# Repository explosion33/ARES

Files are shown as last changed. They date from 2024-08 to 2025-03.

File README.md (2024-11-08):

# ARES
Controls and Electronics Repository for SARP's Autonomous Recovery Experimental System (ARES).

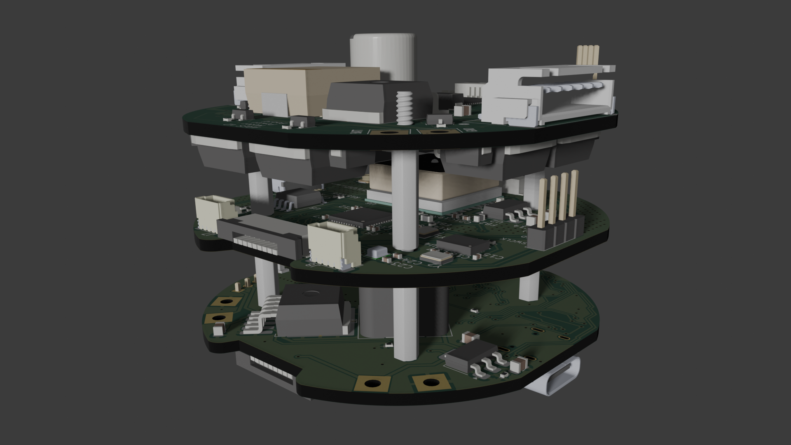
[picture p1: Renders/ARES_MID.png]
ARES Middle Image


## Directory / Ownership

[CC1200 Radio Board / ARES RF Board](https://github.com/stars/explosion33/lists/cc1200-radio-project) | Ethan Armstrong
<br/>
ARES RF board group: KiCad files, Firmware, supporting software

*/CAD*
<br/>
ARES PCB CAD

*/HBridgeTest*
<br/>
HBridge breadboard sample / control code

*/Hardware/Flight_Computer* | Jimmy Fowler
<br/>
ARES Flight Computer PCB Kicad Files

*/Hardware/motor_control_design* | Oliver Buehrer, Ethan Armstrong
<br/>
ARES Actuation (Motor Control) / Power Supply Board Kicad files

*/Renders*
<br/>
ARES PCB Renders

*/Software/Simulation* | Jimmy Fowler
<br/>
ARES simulation code

*/Testbed*
<br/>
ARES Testbed firmware

*/UI*
<br/>
ARES Ground Station UI

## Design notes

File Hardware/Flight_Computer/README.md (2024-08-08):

# RCS_Hardware
SARP 2023 RCS Flight Controller KiCAD project

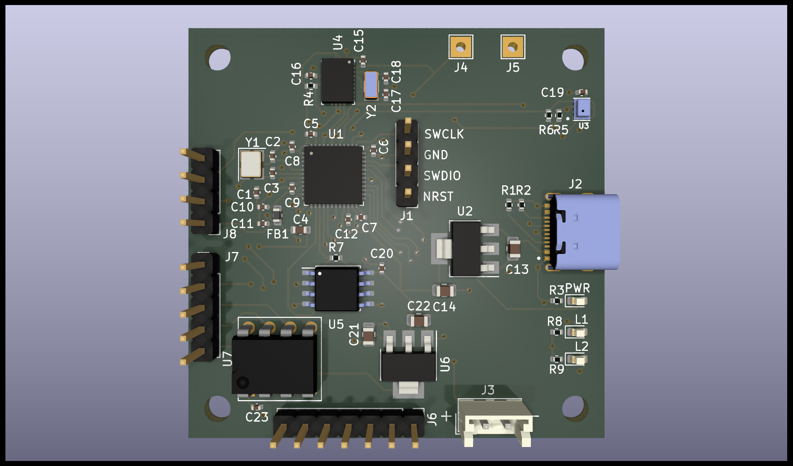
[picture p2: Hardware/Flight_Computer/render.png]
BOARD RENDER


# Components
* STM32F401CCU6
* BNO055
* BMP280
* LIS2HH12 (TODO)
* W25Q32JVXX
* USB-C
* Battery Connector

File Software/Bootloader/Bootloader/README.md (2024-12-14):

# Motor Control / Power Board Testing CodeBase
Codebase in order to test the base functionality of the [MCP Hardware](https://github.com/explosion33/ARES/tree/main/Hardware/motor_control_design)

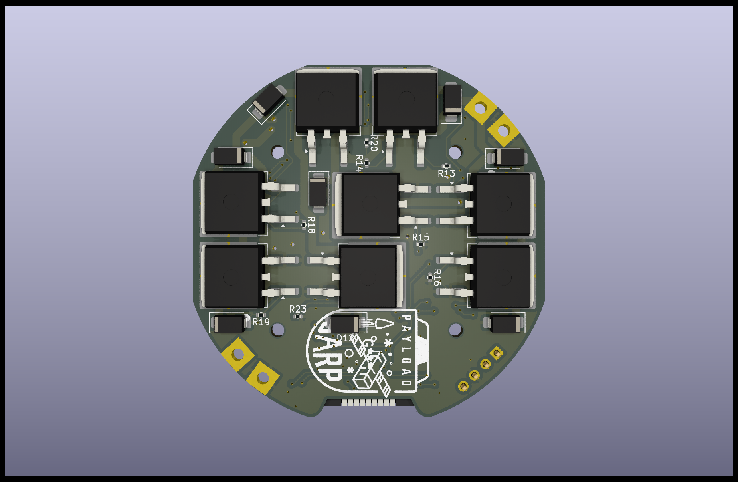
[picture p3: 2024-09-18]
Hardware/motor_control_design/renders/bottom.png

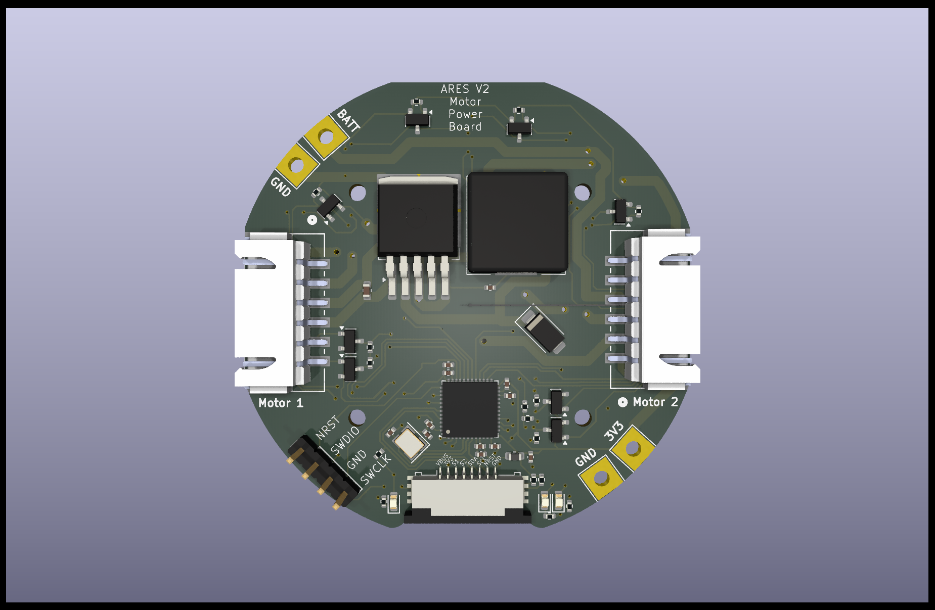
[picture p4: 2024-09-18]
Hardware/motor_control_design/renders/top.png

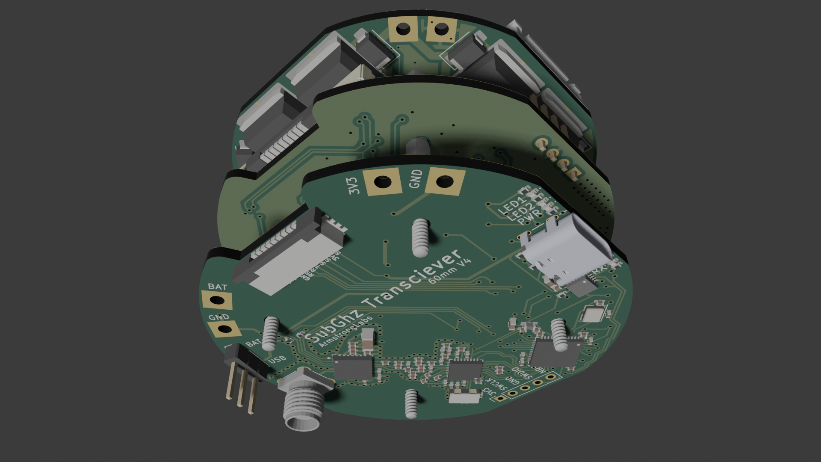
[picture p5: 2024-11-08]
Renders/ARES_BOT.png

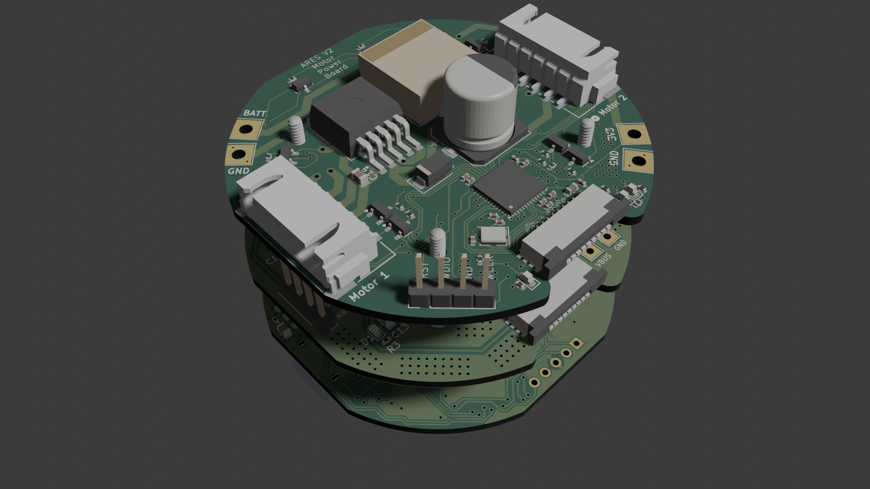
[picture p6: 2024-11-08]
Renders/ARES_TOP.png

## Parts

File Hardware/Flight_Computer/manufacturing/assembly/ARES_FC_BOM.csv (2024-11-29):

Comment | Designator | Footprint | LCSC Part
Antenna | AE1 | Connector_Coaxial:U.FL_Molex_MCRF_73412-0110_Vertical | C5137195
1uF | C10,C11,C21 | Capacitor_SMD:C_0402_1005Metric | C52923
2.2uF | C12 | Capacitor_SMD:C_0402_1005Metric | C12530
22uF | C13,C14 | Capacitor_SMD:C_0805_2012Metric | C5674
22pF | C17,C18 | Capacitor_SMD:C_0402_1005Metric | C466226
10pF | C2,C3 | Capacitor_SMD:C_0402_1005Metric | C32949
10uF | C4 | Capacitor_SMD:C_0603_1608Metric | C19702
100nF | C5,C6,C7,C8,C15,C16,C19,C20,C23,C24 | Capacitor_SMD:C_0402_1005Metric | C307331
10nF | C9 | Capacitor_SMD:C_0402_1005Metric | C15195
LED | D1,D2 | LED_SMD:LED_0603_1608Metric | C12624
LED | D3 | LED_SMD:LED_0603_1608Metric | C2288
LED | D4 | LED_SMD:LED_0603_1608Metric | C2290
120R | FB1 | Inductor_SMD:L_0603_1608Metric | C85831
600R | FB2 | Inductor_SMD:L_0603_1608Metric | C88976
MountingHole | H1,H2,H3,H4 | MountingHole:MountingHole_2.2mm_M2
SWD | J1 | Connector_PinHeader_2.54mm:PinHeader_1x04_P2.54mm_Vertical
TYPE-C-31-M-12 | J2 | USBC:HRO_TYPE-C-31-M-12 | C165948
FC_M/P | J3 | Connector_FFC-FPC:Molex_200528-0080_1x08-1MP_P1.00mm_Horizontal | C132510
5V | J4 | TestPoint:TestPoint_THTPad_2.5x2.5mm_Drill1.2mm
GND | J5 | TestPoint:TestPoint_THTPad_2.5x2.5mm_Drill1.2mm
FC_RF | J6 | Connector_FFC-FPC:Molex_200528-0080_1x08-1MP_P1.00mm_Horizontal | C132510
Conn_01x04_Pin | J7,J8 | Connector_JST:JST_SH_BM04B-SRSS-TB_1x04-1MP_P1.00mm_Vertical | C160390
5.11k | R1,R2 | Resistor_SMD:R_0402_1005Metric | C25906
4.7k | R12,R13,R15,R16 | Resistor_SMD:R_0402_1005Metric | C140158
1k | R3,R8,R9 | Resistor_SMD:R_0402_1005Metric | C11702
10k | R4,R5,R7,R14 | Resistor_SMD:R_0402_1005Metric | C60490
470 | R6,R10,R11 | Resistor_SMD:R_0402_1005Metric | C25167
STM32F401CCU6 | U1 | Package_DFN_QFN:QFN-48-1EP_7x7mm_P0.5mm_EP5.6x5.6mm | C79861
AMS1117-3.3 | U2 | Package_TO_SOT_SMD:SOT-223-3_TabPin2 | C6186
BMP280 | U3 | BMP280:XDCR_BMP280 | C83291
BNO055 | U4 | Package_LGA:LGA-28_5.2x3.8mm_P0.5mm | C93216
W25Q32JVSS | U5 | Package_SO:SOIC-8_5.23x5.23mm_P1.27mm | C82344
PA1616S | U6 | CD-PA1616D:XCVR_CD-PA1616D | C9900146965
16MHz | Y1 | Crystal:Crystal_SMD_3225-4Pin_3.2x2.5mm | C13738
32.768kHz | Y2 | Crystal:Crystal_SMD_3215-2Pin_3.2x1.5mm | C32346

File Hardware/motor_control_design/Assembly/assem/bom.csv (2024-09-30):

Comment | Designator | Footprint | LCSC Part #
10uF Unpolarized capacitor | C1 | C_0402_1005Metric | C19702
10pF Unpolarized capacitor | C2,C5 | C_0402_1005Metric | C32949
100nF Unpolarized capacitor | C3,C4,C6,C8 | C_0402_1005Metric | C307331
2.2uF Unpolarized capacitor | C7 | C_0402_1005Metric | C12530
10nF Unpolarized capacitor | C9 | C_0402_1005Metric | C15195
1uF Unpolarized capacitor | C10,C11 | C_0402_1005Metric | C52923
100uF Unpolarized capacitor | C14 | C_0805_2012Metric | C141660
330uF Unpolarized capacitor | C15 | C_0402_1005Metric | C19702
LED Light emitting diode | D1,D2,D3 | LED_0603_1608Metric | C273598
SS34 40V 3A Schottky Diode, SMA | D4,D5,D6,D7,D8,D9,D10,D11,D12 | D_SMA | C3032484
120R Ferrite bead, small symbol | FB1 | L_0603_1608Metric | C85831
SWD Generic connector, single row, 01x04, script generated (kicad-library-utils/schlib/autogen/connector/) | J2 | PinHeader_1x04_P2.54mm_Vertical
VBAT Generic connector, single row, 01x01, script generated (kicad-library-utils/schlib/autogen/connector/) | J3 | TestPoint_THTPad_4.0x4.0mm_Drill2.0mm
GND Generic connector, single row, 01x01, script generated (kicad-library-utils/schlib/autogen/connector/) | J4,J9 | TestPoint_THTPad_4.0x4.0mm_Drill2.0mm
FC_M/P Generic connector, single row, 01x08, script generated (kicad-library-utils/schlib/autogen/connector/) | J5 | Molex_200528-0080_1x08-1MP_P1.00mm_Horizontal | C124378
Conn_01x06 Generic connector, single row, 01x06, script generated (kicad-library-utils/schlib/autogen/connector/) | J6,J8 | CONN_S6B-XH-SM4-TB_JST
3V3 Generic connector, single row, 01x01, script generated (kicad-library-utils/schlib/autogen/connector/) | J10 | TestPoint_THTPad_4.0x4.0mm_Drill2.0mm
100uH Inductor | L1 | L_12x12mm_H4.5mm | C7431084
RF1S9540SM -74A Id, -55V Vds, Single P-Channel HEXFET Power MOSFET, 20mOhm Ron, TO-220AB | Q1,Q2,Q6,Q14 | TO-263-2 | C33903
IRLZ44NS 47A Id, 55V Vds, 22mOhm Rds Single N-Channel HEXFET Power MOSFET, TO-220AB | Q3,Q7,Q9,Q15 | TO-263-2 | C538199
2N7002 0.115A Id, 60V Vds, N-Channel MOSFET, SOT-23 | Q4,Q5,Q8,Q10,Q11,Q12,Q13,Q16 | SOT-23 | C466660
4.7k Resistor | R1,R2 | R_0402_1005Metric | C174364
10k Resistor | R3,R12 | R_0402_1005Metric | C176114
1k Resistor | R4,R5,R6,R7,R8,R9,R10,R13,R14,R15,R16,R17,R18,R19,R20,R21,R22,R23,R24 | R_0402_1005Metric | C102758
29.4k Resistor | R11 | R_0402_1005Metric | C162880
STM32F401CCU6 ARM Cortex-M4 MCU, 256KB flash, 64KB RAM, 84MHz, 1.7-3.6V, 36 GPIO, UFQFPN-48 | U1 | QFN-48-1EP_7x7mm_P0.5mm_EP5.6x5.6mm | C79861
LM2576S-3.3 3.3V, 3A SIMPLE SWITCHER® Step-Down Voltage Regulator, TO-263 | U3 | TO-263-5_TabPin3 | C347414
16MHz Four pin crystal, GND on pins 2 and 4 | Y1 | Crystal_SMD_3225-4Pin_3.2x2.5mm | C13738

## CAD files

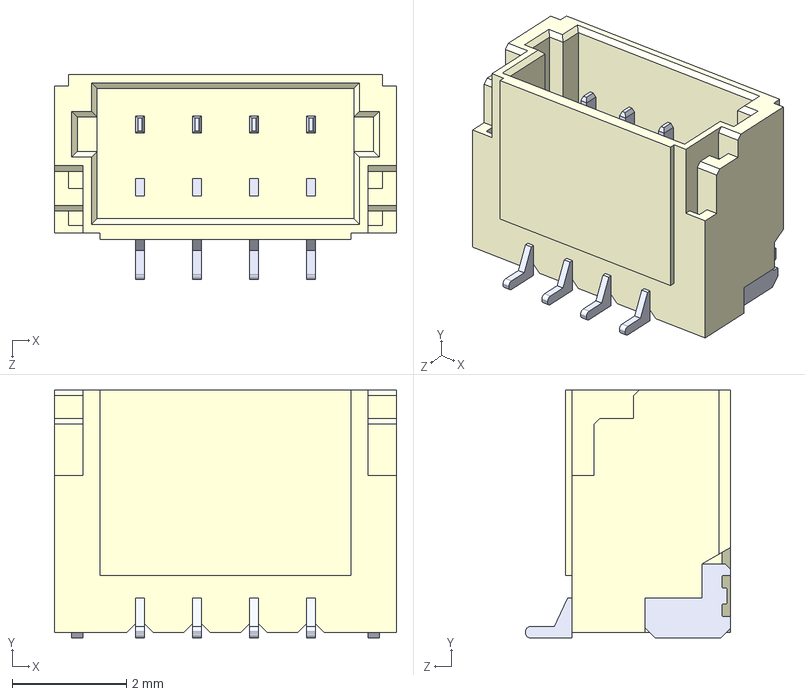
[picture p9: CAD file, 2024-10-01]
Hardware/Flight_Computer/Components/BM04B-SRSS-TB/BM04B-SRSS-TB-LF--SN---3DModel-STEP-56544.STEP
6.00 x 4.35 x 3.60 mm

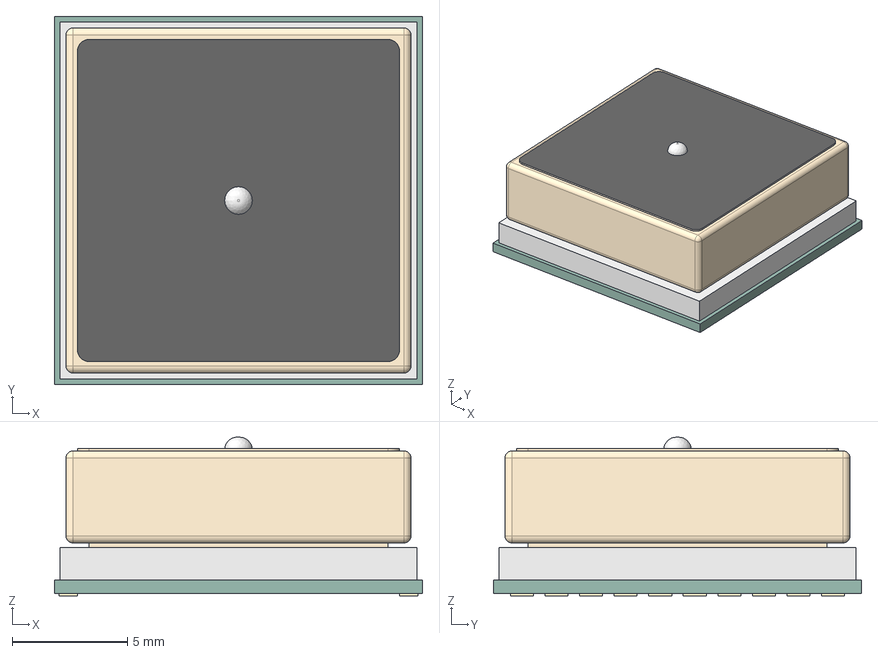
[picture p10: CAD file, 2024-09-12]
Hardware/Flight_Computer/Components/PA1616S/AdafruitGPSv2.step
16.0 x 16.0 x 6.90 mm
Antenna
Shield
PCB
Pads

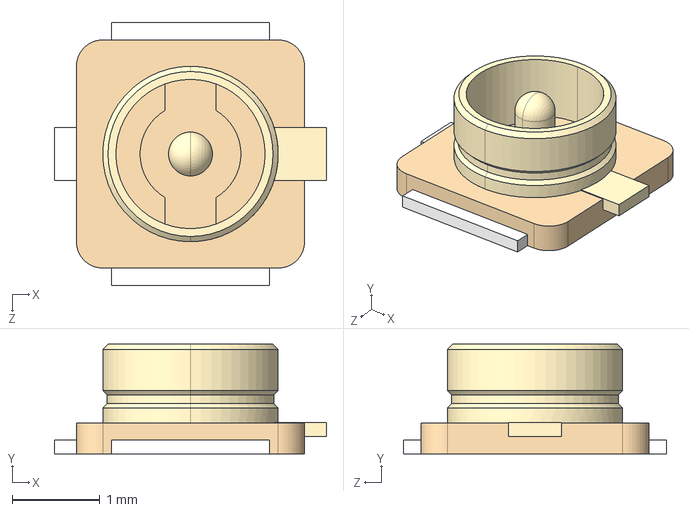
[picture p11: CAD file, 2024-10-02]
Hardware/Flight_Computer/Components/U.FL/U.FL-R-SMT(10)--3DModel-STEP-56544.STEP
3.10 x 1.25 x 3.00 mm

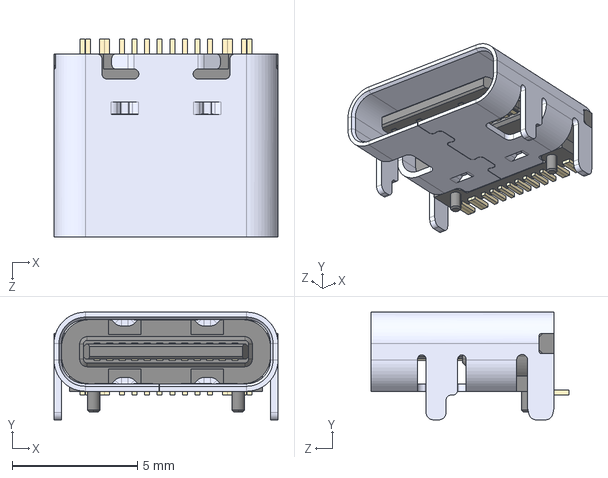
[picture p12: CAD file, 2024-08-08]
Hardware/Flight_Computer/Components/USB-C/TYPE-C-31-M-12.step
8.94 x 4.30 x 7.90 mm

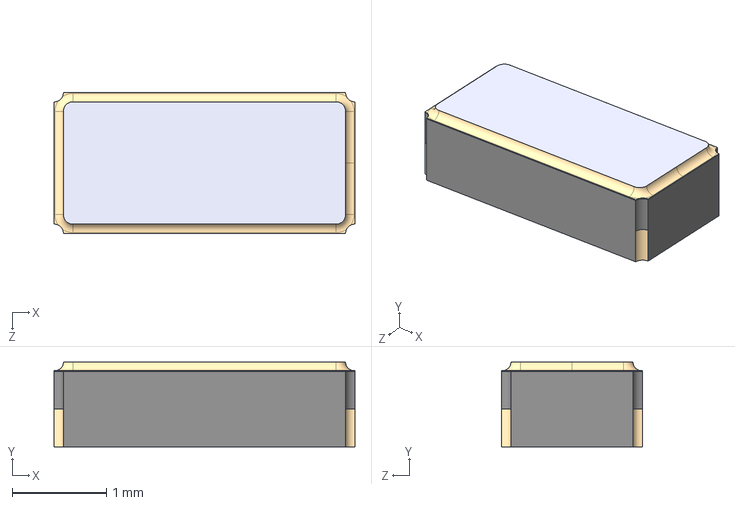
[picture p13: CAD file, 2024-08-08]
Hardware/motor_control_design/Components/32_768_Crystal/32_768_crystal.STEP
3.20 x 0.9 x 1.50 mm

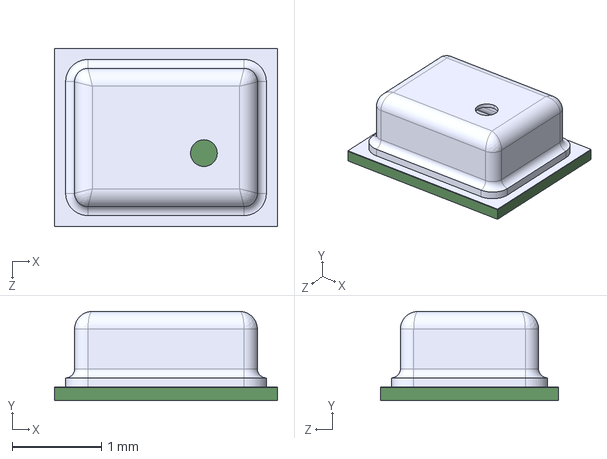
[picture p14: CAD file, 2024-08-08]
Hardware/motor_control_design/Components/BMP280/BMP280.step
2.50 x 1.00 x 2.00 mm

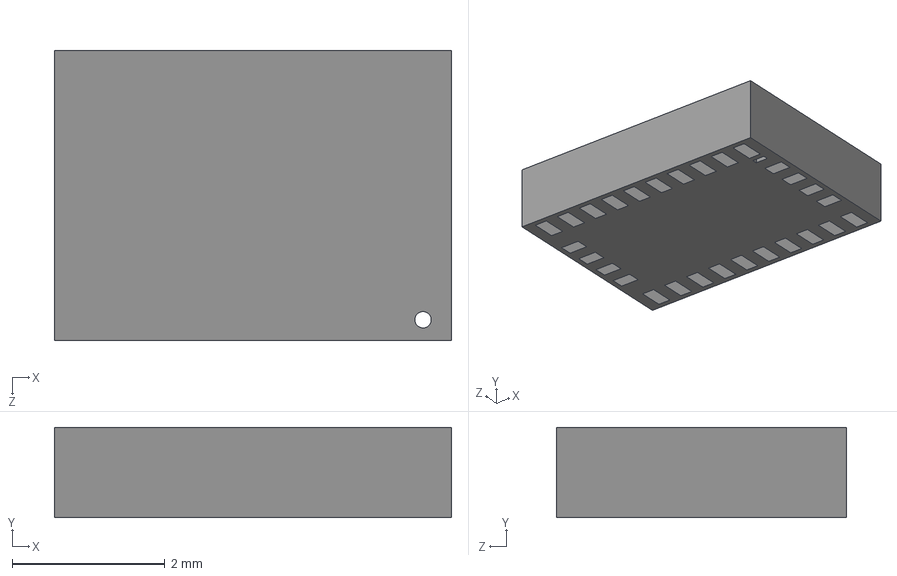
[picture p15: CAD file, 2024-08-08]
Hardware/motor_control_design/Components/BNO055/BNO055.step
5.20 x 1.18 x 3.80 mm

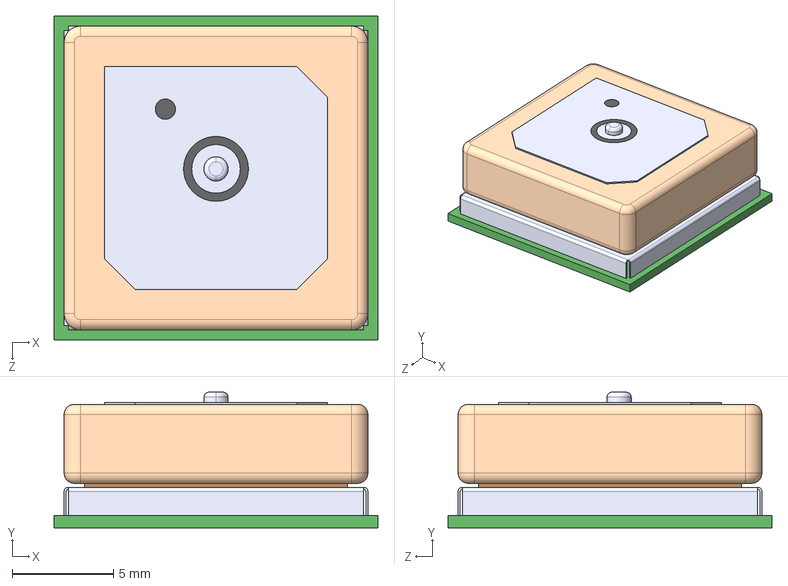
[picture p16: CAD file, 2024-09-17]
Hardware/motor_control_design/Components/CD-PA1616D/CD-PA1616D.step
16.0 x 6.70 x 16.0 mm

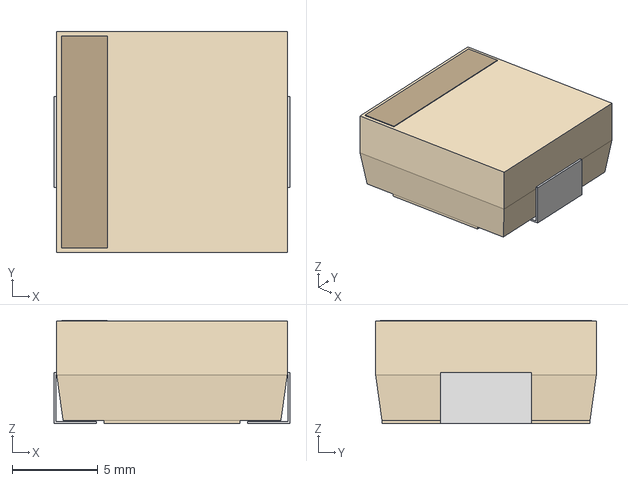
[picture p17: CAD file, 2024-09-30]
Hardware/motor_control_design/Components/IND_MWSA1206S_SNL.step
13.8 x 12.9 x 6.04 mm

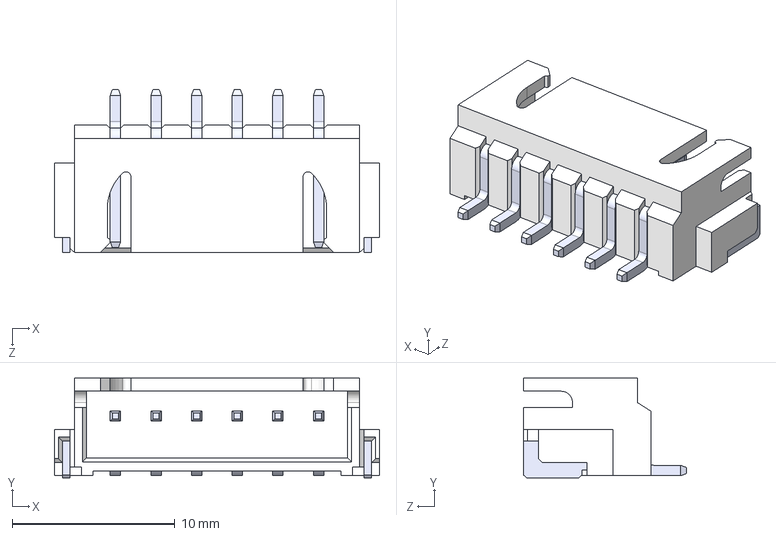
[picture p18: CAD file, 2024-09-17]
Hardware/motor_control_design/Components/JST/KiCADv6/S6B-XH-SM4-TB-LF--SN---3DModel-STEP-56544.STEP
20.0 x 6.12 x 10.0 mm
SxB-XH-SM4-TB_6
pin^SxB-XH-SM4-TB Ass x 6

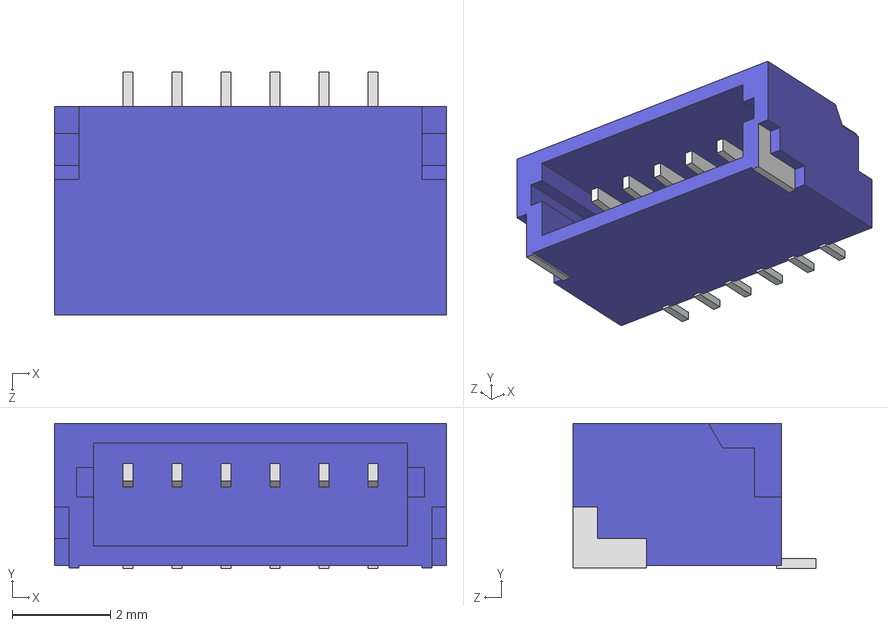
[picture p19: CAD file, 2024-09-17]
Hardware/motor_control_design/Components/JST/SM06B-SRSS-TB.STEP
8.00 x 2.96 x 4.95 mm

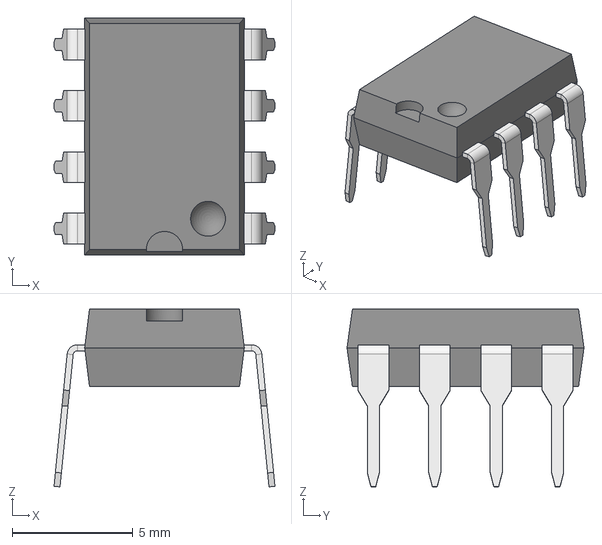
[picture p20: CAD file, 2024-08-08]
Hardware/motor_control_design/Components/LT1690/DIP-8 N.step
9.14 x 9.80 x 7.35 mm

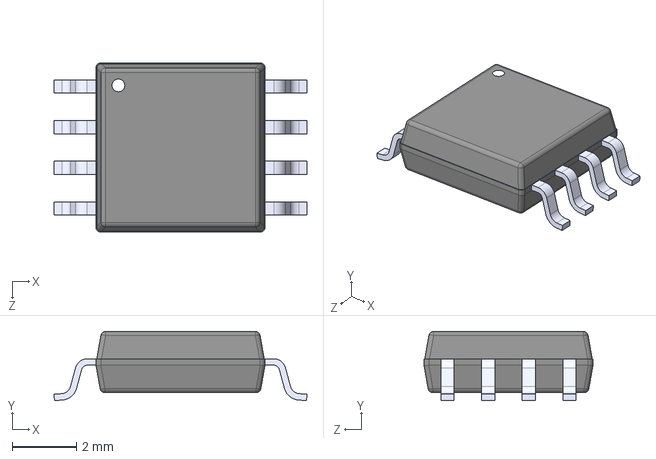
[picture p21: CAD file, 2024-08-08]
Hardware/motor_control_design/Components/W25Q32/W25Q32JVSSIQ--3DModel-STEP-269445.STEP
7.90 x 2.16 x 5.28 mm

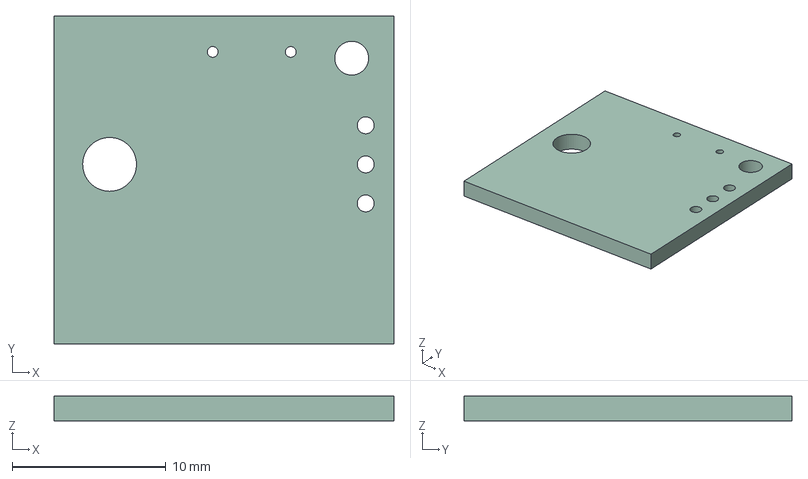
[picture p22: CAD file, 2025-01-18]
Hardware/PullTab/cad/pulltab.step
22.1 x 21.3 x 1.60 mm

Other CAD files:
Hardware/motor_control_design/Components/LT1690/LTC1690IN8#PBF.STEP

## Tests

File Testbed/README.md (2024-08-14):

# TestBed CodeBase
ARES V2 will be based off of [RCS Hardware](https://github.com/explosion33/sarprcs) that was never fully developed last year

RCS boards have been manufactured and will be used as a testbed to confirm initial designs and any changes

This is the code base for those tests

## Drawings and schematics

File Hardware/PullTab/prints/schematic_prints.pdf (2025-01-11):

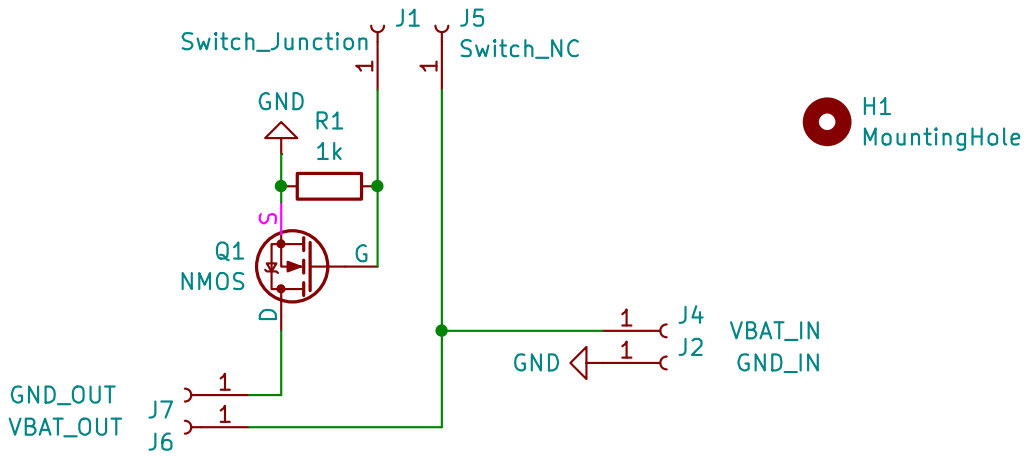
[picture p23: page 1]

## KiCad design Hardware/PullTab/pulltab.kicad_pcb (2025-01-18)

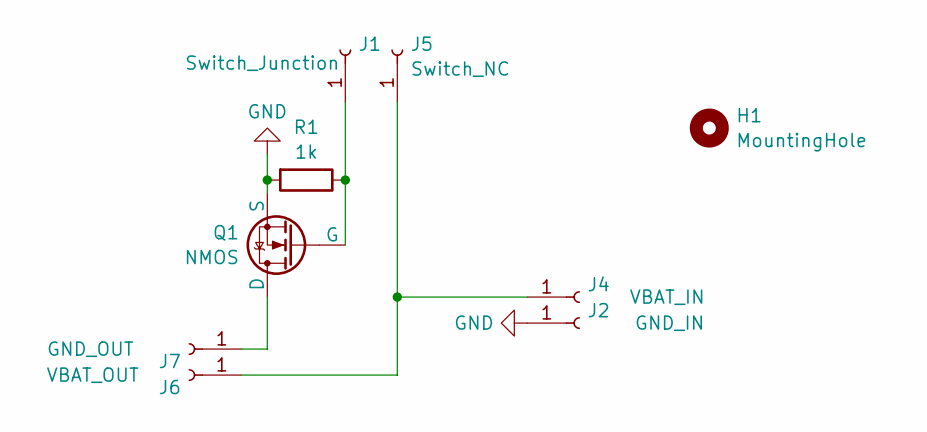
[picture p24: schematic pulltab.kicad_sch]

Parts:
H1: MountingHole; MountingHole_2.2mm_M2
J1: Switch_Junction; TestPoint_Pad_2.5x2.5mm
J2: GND_IN; TestPoint_Pad_4.0x4.0mm
J4: VBAT_IN; TestPoint_Pad_4.0x4.0mm
J5: Switch_NC; TestPoint_Pad_2.5x2.5mm
J6: VBAT_OUT; TestPoint_Pad_4.0x4.0mm
J7: GND_OUT; TestPoint_Pad_4.0x4.0mm
Q1: NMOS; TO-220-3_Horizontal_TabDown
R1: 1k; R_Axial_DIN0204_L3.6mm_D1.6mm_P5.08mm_Horizontal

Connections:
GND: J2.1, Q1.3 (S), R1.2
unnamed: J1.1, Q1.1 (G), R1.1
unnamed: J4.1, J5.1, J6.1
unnamed: J7.1, Q1.2 (D)

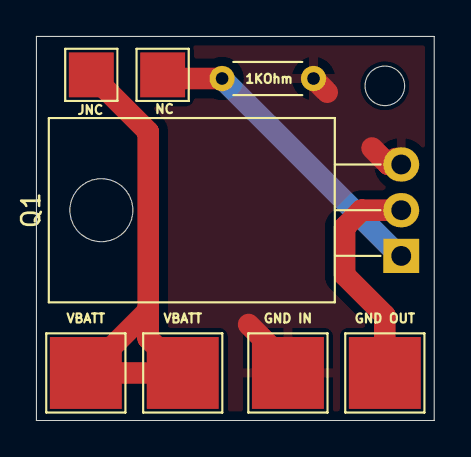
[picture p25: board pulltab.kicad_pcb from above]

Board: 2 copper layers, 22.1 x 21.3 mm, 9 parts (0 on the bottom side), 4 nets.

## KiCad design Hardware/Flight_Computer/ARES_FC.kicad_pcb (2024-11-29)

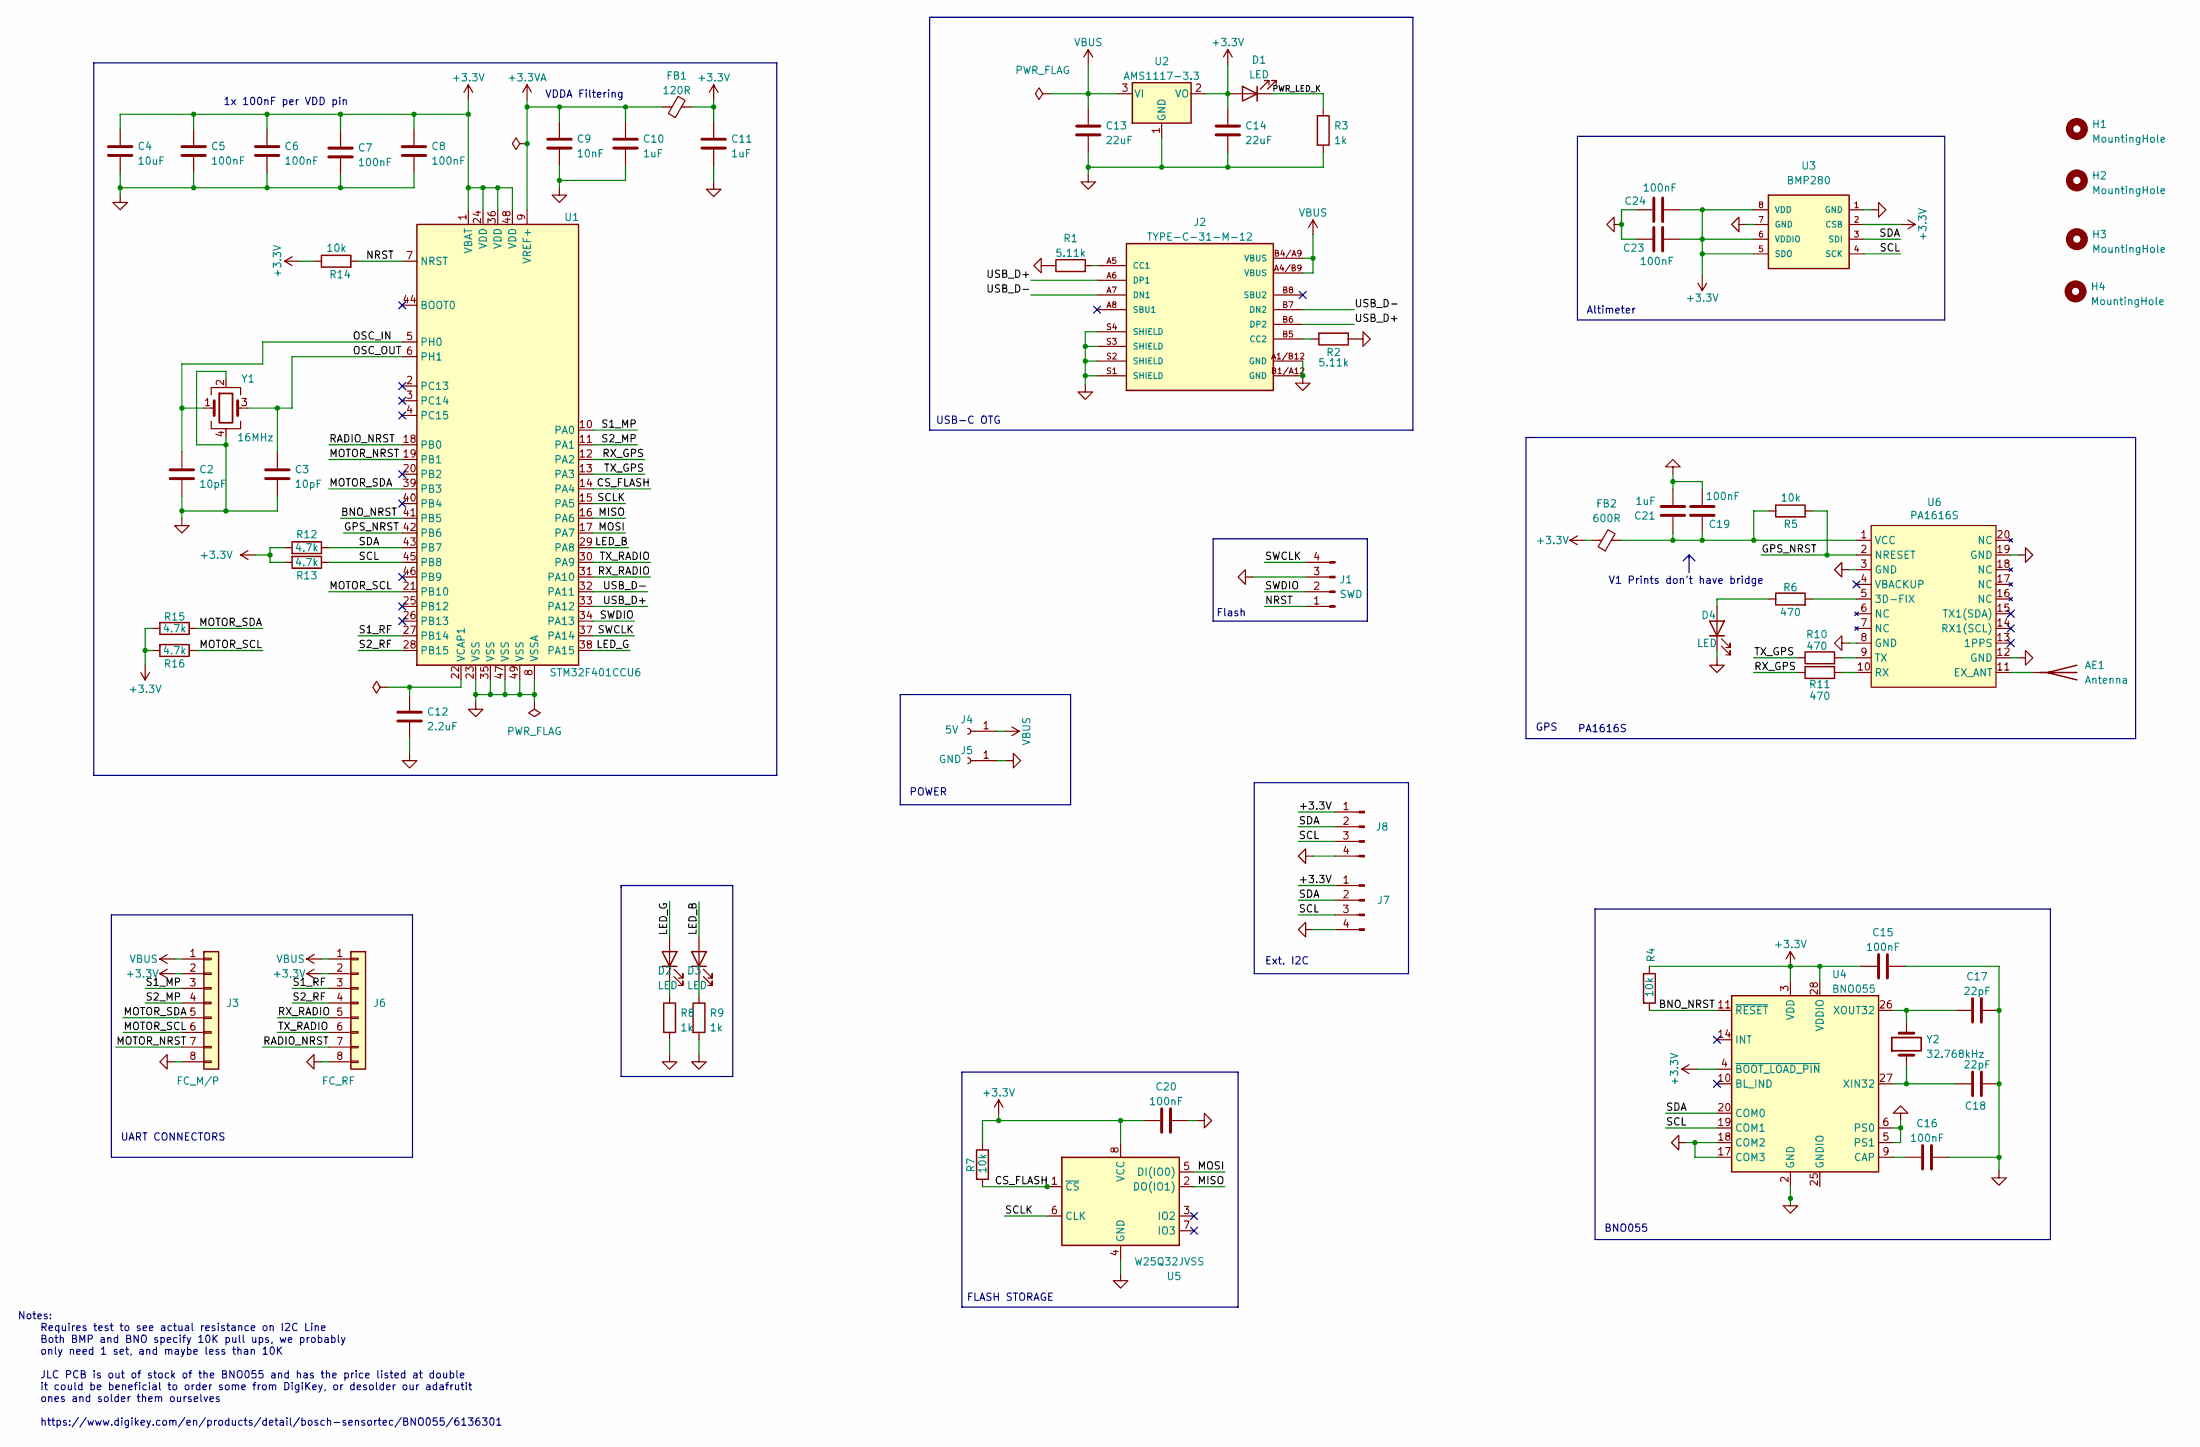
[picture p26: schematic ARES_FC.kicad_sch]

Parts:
AE1: Antenna; U.FL_Molex_MCRF_73412-0110_Vertical; LCSC Part C5137195
C2, C3: 10pF; C_0402_1005Metric; LCSC Part C32949
C4: 10uF; C_0603_1608Metric; LCSC Part C19702
C5, C6, C7, C8, C15, C16, C19, C20, C23, C24: 100nF; C_0402_1005Metric; LCSC Part C307331
C9: 10nF; C_0402_1005Metric; LCSC Part C15195
C10, C11, C21: 1uF; C_0402_1005Metric; LCSC Part C52923
C12: 2.2uF; C_0402_1005Metric; LCSC Part C12530
C13, C14: 22uF; C_0805_2012Metric; LCSC Part C5674
C17, C18: 22pF; C_0402_1005Metric; LCSC Part C466226
D1, D2: LED; LED_0603_1608Metric; LCSC Part C12624
D3: LED; LED_0603_1608Metric; LCSC Part C2288
D4: LED; LED_0603_1608Metric; LCSC Part C2290
FB1: 120R; L_0603_1608Metric; LCSC Part C85831
FB2: 600R; L_0603_1608Metric; LCSC Part C88976
H1, H2, H3, H4: MountingHole; MountingHole_2.2mm_M2
J1: SWD; PinHeader_1x04_P2.54mm_Vertical; LCSC Part C3025061
J2: TYPE-C-31-M-12; HRO_TYPE-C-31-M-12; PARTREV 2020.12.08; LCSC Part C165948
J3: FC_M/P; Molex_200528-0080_1x08-1MP_P1.00mm_Horizontal; LCSC Part C132510
J4: 5V; TestPoint_THTPad_2.5x2.5mm_Drill1.2mm
J5: GND; TestPoint_THTPad_2.5x2.5mm_Drill1.2mm
J6: FC_RF; Molex_200528-0080_1x08-1MP_P1.00mm_Horizontal; LCSC Part C132510
J7, J8: Conn_01x04_Pin; JST_SH_BM04B-SRSS-TB_1x04-1MP_P1.00mm_Vertical; LCSC Part C160390
R1, R2: 5.11k; R_0402_1005Metric; LCSC Part C25906
R3, R8, R9: 1k; R_0402_1005Metric; LCSC Part C11702
R4, R5, R7, R14: 10k; R_0402_1005Metric; LCSC Part C60490
R6, R10, R11: 470; R_0402_1005Metric; LCSC Part 0402WGJ0471TCE
R12, R13, R15, R16: 4.7k; R_0402_1005Metric; LCSC Part C119339
U1: STM32F401CCU6; QFN-48-1EP_7x7mm_P0.5mm_EP5.6x5.6mm; LCSC Part C79861
U2: AMS1117-3.3; SOT-223-3_TabPin2; LCSC Part C6186
U3: BMP280; XDCR_BMP280; PART_REV 1.19; LCSC Part C83291
U4: BNO055; LGA-28_5.2x3.8mm_P0.5mm; LCSC Part C93216
U5: W25Q32JVSS; SOIC-8_5.23x5.23mm_P1.27mm; LCSC Part C82344
U6: PA1616S; XCVR_CD-PA1616D; LCSC Part C9900146965
Y1: 16MHz; Crystal_SMD_3225-4Pin_3.2x2.5mm; LCSC Part C13738
Y2: 32.768kHz; Crystal_SMD_3215-2Pin_3.2x1.5mm; LCSC Part C32346

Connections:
+3.3V: C4.1, C5.1, C6.1, C7.1, C8.1, C11.1, C14.1, C15.1, C20.1, C23.2, C24.2, D1.2 (A), FB1.2, FB2.1, J3.2, J6.2, J7.1, J8.1, R4.1, R7.1, R12.2, R13.2, R14.1, R15.2, R16.2, U1.1 (VBAT), U1.24 (VDD), U1.36 (VDD), U1.48 (VDD), U2.2 (VO), U3.2 (CSB), U3.5 (SDO), U3.6 (VDDIO), U3.8 (VDD), U4.3 (VDD), U4.4 (~BOOT_LOAD_PIN), U4.28 (VDDIO), U5.8 (VCC)
+3.3VA: C9.1, C10.1, FB1.1, U1.9 (VREF+)
/BNO_NRST: R4.2, U1.41 (PB5), U4.11 (~RESET)
/CS_FLASH: R7.2, U1.14 (PA4), U5.1 (~CS)
/GPS_NRST: R5.2, U1.42 (PB6), U6.2 (NRESET)
/LED_B: D3.2 (A), U1.29 (PA8)
/LED_G: D2.2 (A), U1.38 (PA15)
/MISO: U1.16 (PA6), U5.2 (DO(IO1))
/MOSI: U1.17 (PA7), U5.5 (DI(IO0))
/MOTOR_NRST: J3.7, U1.19 (PB1)
/MOTOR_SCL: J3.6, R16.1, U1.21 (PB10)
/MOTOR_SDA: J3.5, R15.1, U1.39 (PB3)
/NRST: J1.1, R14.2, U1.7 (NRST); also elsewhere on the board
/OSC_IN: C2.1, U1.5 (PH0), Y1.1
/OSC_OUT: C3.1, U1.6 (PH1), Y1.3
/PWR_LED_K: D1.1 (K), R3.1
/RADIO_NRST: J6.7, U1.18 (PB0)
/RX_GPS: R11.1, U1.12 (PA2)
/RX_RADIO: J6.5, U1.31 (PA10)
/S1_MP: J3.3, U1.10 (PA0)
/S1_RF: J6.3, U1.27 (PB14)
/S2_MP: J3.4, U1.11 (PA1)
/S2_RF: J6.4, U1.28 (PB15)
/SCL: J7.3, J8.3, R13.1, U1.45 (PB8), U3.4 (SCK), U4.19 (COM1)
/SCLK: U1.15 (PA5), U5.6 (CLK)
/SDA: J7.2, J8.2, R12.1, U1.43 (PB7), U3.3 (SDI), U4.20 (COM0)
/SWCLK: J1.4, U1.37 (PA14)
/SWDIO: J1.2, U1.34 (PA13)
/TX_GPS: R10.1, U1.13 (PA3)
/TX_RADIO: J6.6, U1.30 (PA9)
/USB_D+: J2.A6 (DP1), J2.B6 (DP2), U1.33 (PA12)
/USB_D-: J2.A7 (DN1), J2.B7 (DN2), U1.32 (PA11)
GND: C2.2, C3.2, C4.2, C5.2, C6.2, C7.2, C8.2, C9.2, C10.2, C11.2, C12.2, C13.2, C14.2, C15.2, C16.2, C17.2, C18.2, C19.2, C20.2, C21.2, C23.1, C24.1, D4.1 (K), J1.3, J2.A1/B12 (GND), J2.B1/A12 (GND), J2.S1 (SHIELD), J2.S2 (SHIELD), J2.S3 (SHIELD), J2.S4 (SHIELD), J3.8, J5.1, J6.8, J7.4, J8.4, R1.1, R2.1, R3.2, R8.2, R9.2, U1.8 (VSSA), U1.23 (VSS), U1.35 (VSS), U1.47 (VSS), U1.49 (VSS), U2.1 (GND), U3.1 (GND), U3.7 (GND), U4.2 (GND), U4.5 (PS1), U4.6 (PS0), U4.17 (COM3), U4.18 (COM2), U5.4 (GND), U6.3 (GND), U6.8 (GND), U6.12 (GND), U6.19 (GND), Y1.2, Y1.4; also elsewhere on the board
unnamed: AE1.1 (A), U6.11 (EX_ANT)
unnamed: D2.1 (K), R8.1
unnamed: D3.1 (K), R9.1
unnamed: D4.2 (A), R6.1
unnamed: J2.A5 (CC1), R1.2
unnamed: J2.B5 (CC2), R2.2
unnamed: C12.1, U1.22 (VCAP1)
unnamed: C16.1, U4.9 (CAP)
unnamed: U4.15 (GNDIO), U4.16 (GNDIO), U4.25 (GNDIO)
unnamed: C18.1, U4.27 (XIN32), Y2.1
unnamed: C17.1, U4.26 (XOUT32), Y2.2
unnamed: R6.2, U6.5 (3D-FIX)
unnamed: R11.2, U6.10 (RX)
unnamed: R10.2, U6.9 (TX)
unnamed: C19.1, C21.1, FB2.2, R5.1, U6.1 (VCC)
VBUS: C13.1, J2.A4/B9 (VBUS), J2.B4/A9 (VBUS), J3.1, J4.1, J6.1, U2.3 (VI)

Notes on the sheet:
VDDA Filtering
Flash
Altimeter
FLASH STORAGE
PA1616S
V1 Prints don't have bridge
1x 100nF per VDD pin
Notes: Requires test to see actual resistance on I2C Line Both BMP and BNO specify 10K pull ups, we probably only need 1 set, and maybe less than 10K JLC PCB is out of stock of the BNO055 and has the price listed at double it could be beneficial to order some from DigiKey, or desolder our adafrutit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
USB-C OTG
GPS
UART CONNECTORS
BNO055
Ext. I2C
POWER

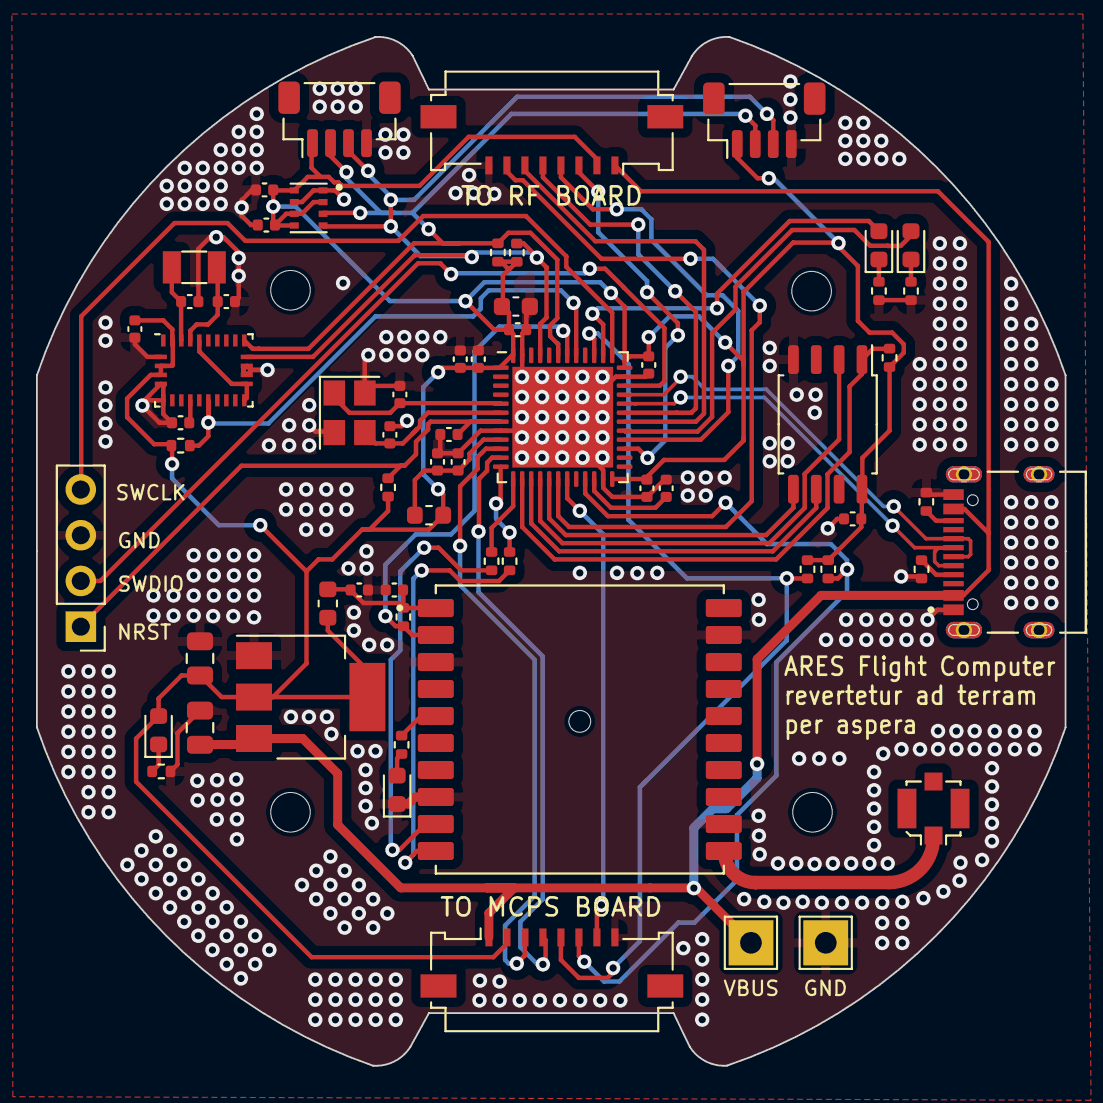
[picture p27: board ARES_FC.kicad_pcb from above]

Board: 2 copper layers, 57.2 x 57.2 mm, 66 parts (0 on the bottom side), 49 nets.

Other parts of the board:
C1: 100nF; C_0402_1005Metric

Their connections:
/NRST: C1.1; also elsewhere on the board
GND: C1.2; also elsewhere on the board

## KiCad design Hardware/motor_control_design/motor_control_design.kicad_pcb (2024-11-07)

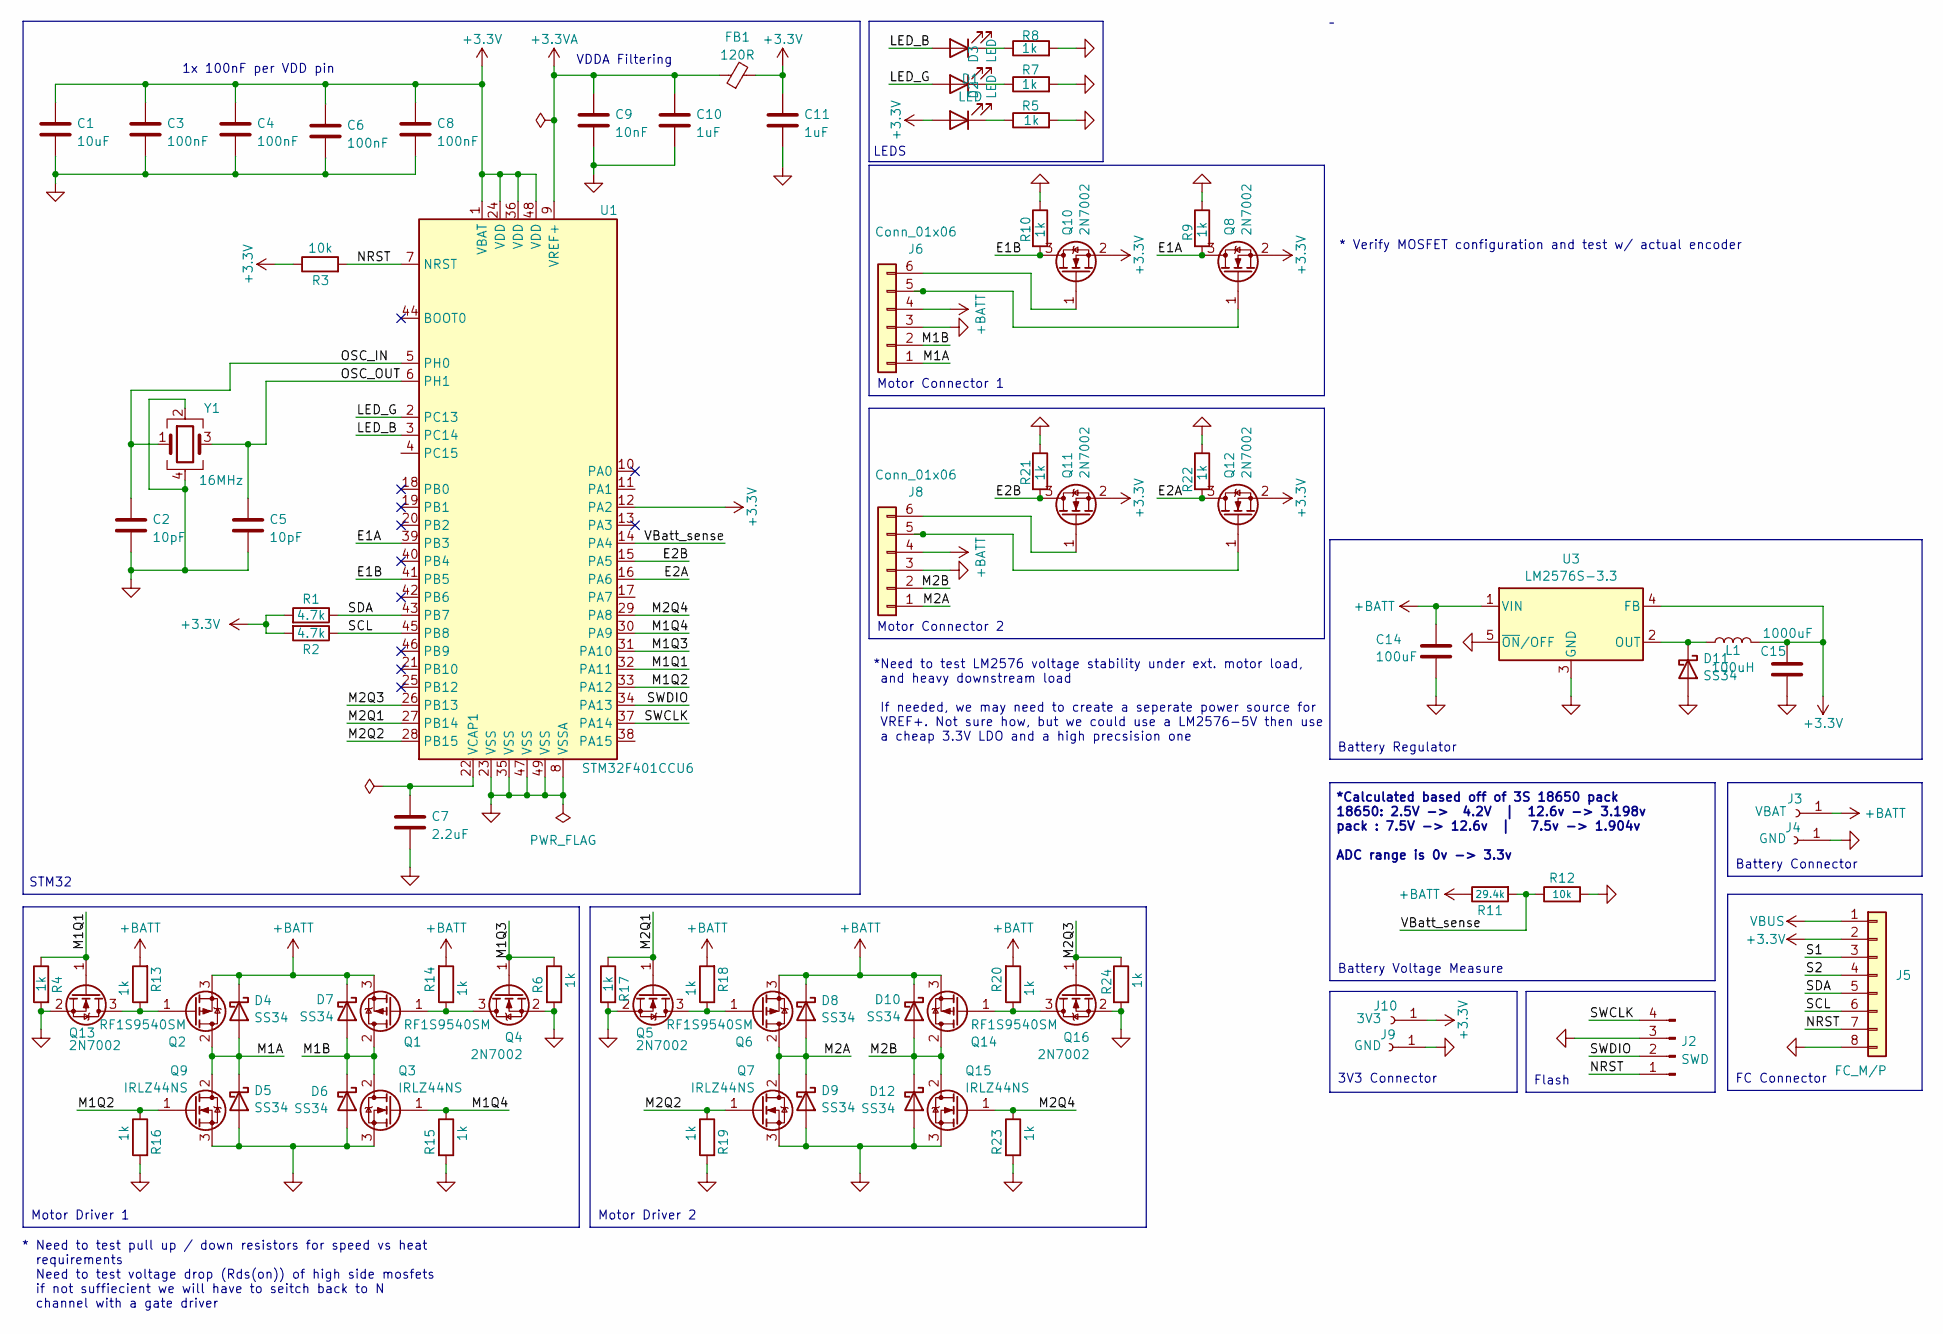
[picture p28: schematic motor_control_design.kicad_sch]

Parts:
C1: 10uF; C_0402_1005Metric; LCSC Part C19702
C2, C5: 10pF; C_0402_1005Metric; LCSC Part C32949
C3, C4, C6, C8: 100nF; C_0402_1005Metric; LCSC Part C307331
C7: 2.2uF; C_0402_1005Metric; LCSC Part C12530
C9: 10nF; C_0402_1005Metric; LCSC Part C15195
C10, C11: 1uF; C_0402_1005Metric; LCSC Part C52923
C14: 100uF; C_0805_2012Metric; LCSC Part C141660
C15: 1000uF; CP_Elec_10x10.5; LCSC Part C189257
D1: LED; LED_0603_1608Metric; LCSC Part C2286
D2: LED; LED_0603_1608Metric; LCSC Part C779453
D3: LED; LED_0603_1608Metric; LCSC Part C131286
D4, D5, D6, D7, D8, D9, D10, D11, D12: SS34; D_SMA; LCSC Part C3032484
FB1: 120R; L_0603_1608Metric; LCSC Part C85831
J2: SWD; PinHeader_1x04_P2.54mm_Vertical
J3: VBAT; TestPoint_THTPad_4.0x4.0mm_Drill2.0mm
J4, J9: GND; TestPoint_THTPad_4.0x4.0mm_Drill2.0mm
J5: FC_M/P; Molex_200528-0080_1x08-1MP_P1.00mm_Horizontal; LCSC Part C132510
J6, J8: Conn_01x06; CONN_S6B-XH-SM4-TB_JST
J10: 3V3; TestPoint_THTPad_4.0x4.0mm_Drill2.0mm
L1: 100uH; L_TaiTech_TMPC1265_13.5x12.5mm; LCSC Part C408533
Q1, Q2, Q6, Q14: RF1S9540SM; TO-263-2; LCSC Part C33903
Q3, Q7, Q9, Q15: IRLZ44NS; TO-263-2; LCSC Part C538199
Q4, Q5, Q8, Q10, Q11, Q12, Q13, Q16: 2N7002; SOT-23; LCSC Part C466660
R1, R2: 4.7k; R_0402_1005Metric; LCSC Part C174364
R3, R12: 10k; R_0402_1005Metric; LCSC Part C176114
R4, R5, R6, R7, R8, R9, R10, R13, R14, R15, R16, R17, R18, R19, R20, R21, R22, R23, R24: 1k; R_0402_1005Metric; LCSC Part C102758
R11: 29.4k; R_0402_1005Metric; LCSC Part C162880
U1: STM32F401CCU6; QFN-48-1EP_7x7mm_P0.5mm_EP5.6x5.6mm; LCSC Part C79861
U3: LM2576S-3.3; TO-263-5_TabPin3; LCSC Part C347412
Y1: 16MHz; Crystal_SMD_3225-4Pin_3.2x2.5mm; LCSC Part C13738

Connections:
+3.3V: C1.1, C3.1, C4.1, C6.1, C8.1, C11.1, C15.2, D1.2 (A), FB1.2, J5.2, J8.7, J8.8, J10.1, L1.2, Q8.2 (S), Q10.2 (S), Q11.2 (S), Q12.2 (S), R1.2, R2.2, R3.1, U1.1 (VBAT), U1.12 (PA2), U1.24 (VDD), U1.36 (VDD), U1.48 (VDD), U3.4 (FB)
+3.3VA: C9.1, C10.1, FB1.1, U1.9 (VREF+)
+BATT: C14.2, D4.1 (K), D7.1 (K), D8.1 (K), D10.1 (K), J3.1, J6.4, J8.4, Q1.3 (S), Q2.3 (S), Q6.3 (S), Q14.3 (S), R11.1, R13.2, R14.2, R18.2, R20.2, U3.1 (VIN)
/E1A: Q8.3 (D), R9.2, U1.39 (PB3)
/E1B: Q10.3 (D), R10.2, U1.41 (PB5)
/E2A: Q12.3 (D), R22.2, U1.16 (PA6)
/E2B: Q11.3 (D), R21.2, U1.15 (PA5)
/LED_B: D3.2 (A), U1.3 (PC14)
/LED_G: D2.2 (A), U1.2 (PC13)
/M1A: D4.2 (A), D5.1 (K), J6.1, Q2.2 (D), Q9.2 (D)
/M1B: D6.1 (K), D7.2 (A), J6.2, Q1.2 (D), Q3.2 (D)
/M1Q1: Q13.1 (G), R4.1, U1.32 (PA11)
/M1Q2: Q9.1 (G), R16.1, U1.33 (PA12)
/M1Q3: Q4.1 (G), R6.1, U1.31 (PA10)
/M1Q4: Q3.1 (G), R15.1, U1.30 (PA9)
/M2A: D8.2 (A), D9.1 (K), J8.1, Q6.2 (D), Q7.2 (D)
/M2B: D10.2 (A), D12.1 (K), J8.2, Q14.2 (D), Q15.2 (D)
/M2Q1: Q5.1 (G), R17.1, U1.27 (PB14)
/M2Q2: Q7.1 (G), R19.1, U1.28 (PB15)
/M2Q3: Q16.1 (G), R24.1, U1.26 (PB13)
/M2Q4: Q15.1 (G), R23.1, U1.29 (PA8)
/NRST: J2.1, J5.7, R3.2, U1.7 (NRST)
/OSC_IN: C2.1, U1.5 (PH0), Y1.1
/OSC_OUT: C5.1, U1.6 (PH1), Y1.3
/S1: J5.3
/S2: J5.4
/SCL: J5.6, R2.1, U1.45 (PB8)
/SDA: J5.5, R1.1, U1.43 (PB7)
/SWCLK: J2.4, U1.37 (PA14)
/SWDIO: J2.2, U1.34 (PA13)
/VBatt_sense: R11.2, R12.1, U1.14 (PA4)
GND: C1.2, C2.2, C3.2, C4.2, C5.2, C6.2, C7.2, C8.2, C9.2, C10.2, C11.2, C14.1, C15.1, D5.2 (A), D6.2 (A), D9.2 (A), D11.2 (A), D12.2 (A), J2.3, J4.1, J5.8, J6.3, J8.3, J9.1, Q3.3 (S), Q4.2 (S), Q5.2 (S), Q7.3 (S), Q9.3 (S), Q13.2 (S), Q15.3 (S), Q16.2 (S), R4.2, R5.2, R6.2, R7.2, R8.2, R9.1, R10.1, R12.2, R15.2, R16.2, R17.2, R19.2, R21.1, R22.1, R23.2, R24.2, U1.8 (VSSA), U1.23 (VSS), U1.35 (VSS), U1.47 (VSS), U1.49 (VSS), U3.3 (GND), U3.5 (~ON/OFF), Y1.2, Y1.4
unnamed: D1.1 (K), R5.1
unnamed: D2.1 (K), R7.1
unnamed: D3.1 (K), R8.1
unnamed: D11.1 (K), L1.1, U3.2 (OUT)
unnamed: J6.5, Q8.1 (G)
unnamed: J6.6, Q10.1 (G)
unnamed: J8.5, Q12.1 (G)
unnamed: J8.6, Q11.1 (G)
unnamed: Q1.1 (G), Q4.3 (D), R14.1
unnamed: Q5.3 (D), Q6.1 (G), R18.1
unnamed: Q2.1 (G), Q13.3 (D), R13.1
unnamed: Q14.1 (G), Q16.3 (D), R20.1
unnamed: C7.1, U1.22 (VCAP1)
VBUS: J5.1

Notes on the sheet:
Battery Regulator
Motor Driver 1
* Verify MOSFET configuration and test w/ actual encoder
Motor Connector 1
* Need to test pull up / down resistors for speed vs heat requirements Need to test voltage drop (Rds(on)) of high side mosfets if not suffiecient we will have to seitch back to N channel with a gate driver
*Calculated based off of 3S 18650 pack 18650: 2.5V -> 4.2V | 12.6v -> 3.198v pack : 7.5V -> 12.6v | 7.5v -> 1.904v ADC range is 0v -> 3.3v
Motor Connector 2
Motor Driver 2
*Need to test LM2576 voltage stability under ext. motor load, and heavy downstream load If needed, we may need to create a seperate power source for VREF+. Not sure how, but we could use a LM2576-5V then use a cheap 3.3V LDO and a high precsision one
Battery Connector
Battery Voltage Measure
VDDA Filtering
Flash
1x 100nF per VDD pin
FC Connector
3V3 Connector
LEDS
STM32

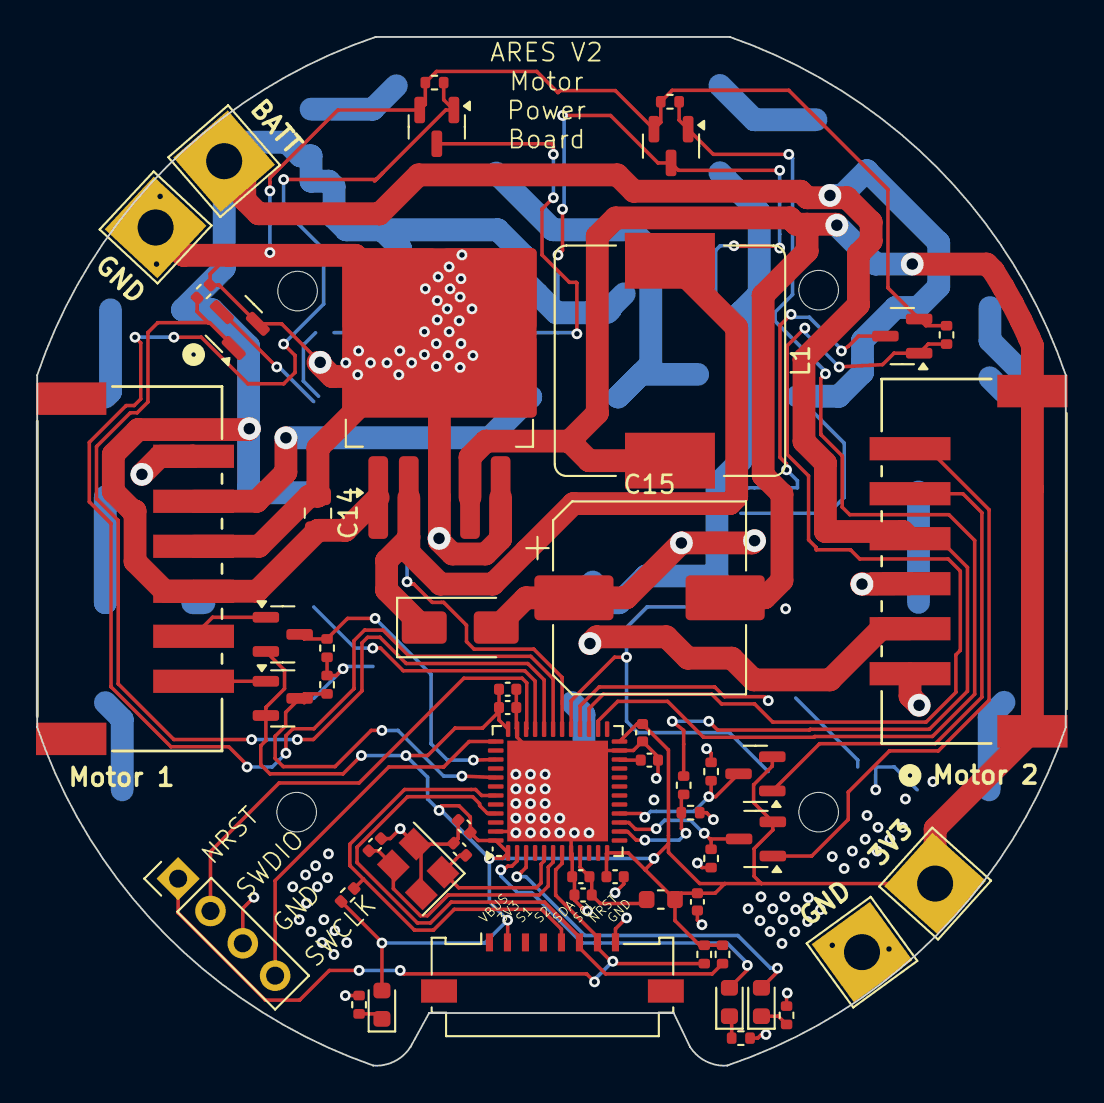
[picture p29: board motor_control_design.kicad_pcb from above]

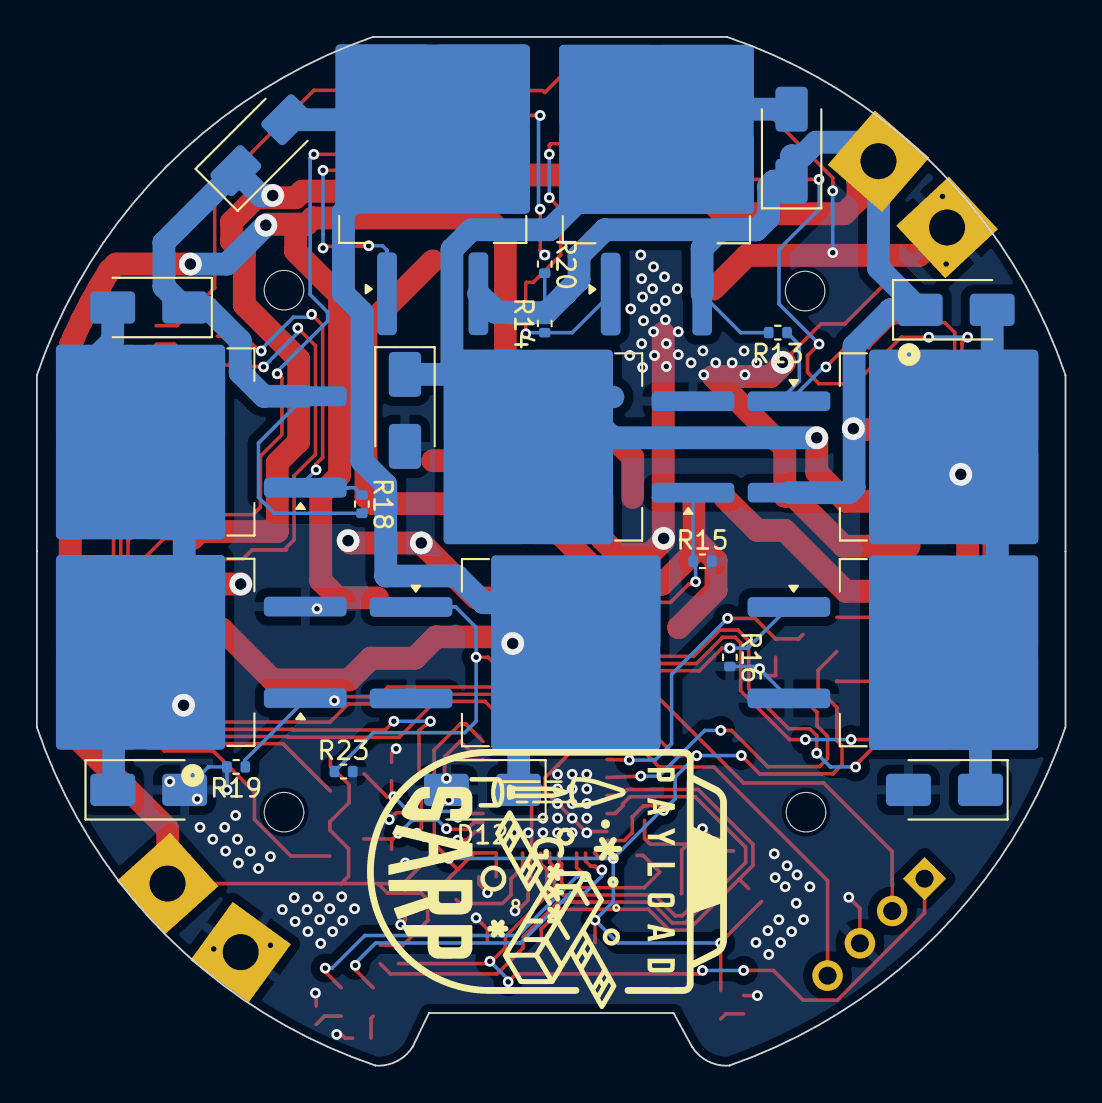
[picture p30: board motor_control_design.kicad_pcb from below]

Board: 2 copper layers, 57.1 x 57.2 mm, 78 parts (24 on the bottom side), 43 nets.

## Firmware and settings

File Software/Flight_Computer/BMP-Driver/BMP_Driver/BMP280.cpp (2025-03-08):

#include"mbed.h"
#include"BMP280.h" 
#include"BMP280_const.h" 
#include<map> 
#include<iostream>
using namespace std;

/* Constructor 
 * @param Pin address of the SDA Pin on the processor 
 * @param Pin address of the SCL Pin on the processor    
 * @param The I2C address for the BMP280
 */
BMP280::BMP280(PinName SDA, PinName SCL, char addr){ 
    owned = true; 
    BMP280::i2c = new I2C(SDA,SCL);
    BMP280::addr = addr; 
}

/* Destructor
 * Deletes I2C if created in object
 */ 
BMP280::~BMP280() {
    if(owned){
        delete i2c; 
    }
}

/*
 * @brief Reads a chunk of data from the BNO055 over I2C.
 * @param regaddr The register address to read from
 * @param data Pointer to a buffer for storing data
 * @param len Number of bytes to read
 * @return 0 on success, non-zero on failure
 */
int BMP280::readData(char regaddr, char* data, uint8_t len) {
    i2c->write(addr, &regaddr, 1);
    return i2c->read(addr, data, len);
}

/* @brief Writes data to a BNO055 register over I2C.
 * @param regaddr The register address to write to
 * @param data The value to be written
 * @return 0 on success, non-zero on failure
 */
int BMP280::writeData(char regaddr, char data) {
    char buffer[2];
    buffer[0] = regaddr;
    buffer[1] = data;
    return i2c->write(addr, buffer, 2);
}

/* @brief Retrieves and organizes temperature data
 * @return calulated temperature value
 */ 
int BMP280::updateTemperatureData(){
    char xlsb, lsb, msb; 
    int msbErr, lsbErr, xlsbErr; 
    xlsbErr = readData(BMP280_TEMP_XLSB, &xlsb, 1);
    lsbErr = readData(BMP280_TEMP_LSB, &lsb, 1);
    msbErr = readData(BMP280_TEMP_MSB, &msb, 1);
    
    int total = xlsbErr + lsbErr + msbErr;
    //Shifts each byte into useful position
    int32_t rawTemperature = ((int32_t)msb << 12) | ((int32_t)lsb << 4 ) | ((int32_t)xlsb >> 4);
    // float temp = ((float)rawTemperature * 9.0/5.0) + 32.0; // Convert from native Celcius to Farienheit
    values.temp_f = convert_temp(rawTemperature);
    return total; 
}

/* @brief Retrieves and organizes pressure data
 * @return calulated pressure value
 */ 
int BMP280::updatePressureData(){
    char xlsb, lsb, msb;
    int msbErr, lsbErr, xlsbErr; 
    xlsbErr = readData(BMP280_PRESS_XLSB, &xlsb, 1); // Extra least significant byte 
    lsbErr = readData(BMP280_PRESS_LSB, &lsb, 1);// Least significant byte 
    msbErr = readData(BMP280_PRESS_MSB, &msb, 1); // Most significant byte 
    int total = xlsbErr + lsbErr + msbErr;

    // Shifts each byte into useful position 
    uint32_t rawPressure = ((uint32_t)msb << 12) | ((uint32_t)lsb << 4 ) | ((uint32_t)xlsb >> 4);
    // float press = (float)rawPressure * 0.0145037738; // Convert from native Hectopascal to psi 
    values.press_psi = BMP280_compensate_P_double(rawPressure); 

    return total; 
}

double BMP280::convert_temp(int32_t adc_T){
    int err = BMP280_CalibrateTemp();

    double var1, var2, T;
    var1 = (((double)adc_T)/16384.0 - ((double)c.dig_T1)/1024.0) * ((double)c.dig_T2);
    var2 = ((((double)adc_T)/131072.0 - ((double)c.dig_T1)/8192.0) * 
    (((double)adc_T)/131072.0 - ((double)c.dig_T1)/8192.0)) * ((double)c.dig_T3);
    t_fine = (int32_t)(var1 + var2);
    T = (var1 + var2)/5120.0;
    return T;
}

// @breif returns pressure data
float BMP280::getPressure(){
    return values.press_psi;
}

double BMP280::BMP280_compensate_P_double(int32_t adc_P){
    int err = BMP280_CalibratePress(); 

    double var1, var2, p;
    var1 = ((double)t_fine/2.0) - 64000.0;
    var2 = var1 * var1 * ((double)c.dig_P6) / 32768.0;
    var2 = var2 + var1 * ((double)c.dig_P5) * 2.0;
    var2 = (var2/4.0)+(((double)c.dig_P4) * 65536.0);
    var1 = (((double)c.dig_P3) * var1 * var1 / 524288.0 + ((double)c.dig_P2) * var1) / 524288.0;
    var1 = (1.0 + var1 / 32768.0)*((double)c.dig_P1);
    if (var1 == 0.0){
        return 0; // avoid exception caused by division by zero
    }
    p = 1048576.0 - (double)adc_P;
    p = (p - (var2 / 4096.0)) * 6250.0 / var1;
    var1 = ((double)c.dig_P9) * p * p / 2147483648.0;
    var2 = p * ((double)c.dig_P8) / 32768.0;
    p = p + (var1 + var2 + ((double)c.dig_P7)) / 16.0;
    return p;
}



// @brief returns temperature value
float BMP280::getTemperature(){
    return values.temp_f;
}

// @breif updates sensor values 
int BMP280::updateValues(){
    int errPress  = updatePressureData();
    int errTemp = updateTemperatureData();
    return(errPress + errTemp);
}

/* @breif check for error from the pressure reading
*/
BMP280_Status BMP280::getPressureStatus() {
 return BMP280_Status::Ok; 
}

//@briif calibrates temperature values
// - Array Calib: each calibration number comes in a lsb and msb pair 
int BMP280::BMP280_CalibrateTemp(){
    char calib[6];
    readData(0x88, calib, 6);
    c.dig_T1 = calib[1] << 8 | calib[0];
    c.dig_T2 = (calib[3] << 8 | calib[2]);
    c.dig_T3 = (calib[5] << 8 | calib[4]);
    return 0;
}

int BMP280::BMP280_CalibratePress(){
    char calib[18];

    // Read Calibration data 
    readData(0x8E, calib, 18);

    // int t1 = readData(0x8E, &calib[0],1);
    // int t2 = readData(0x8F, &calib[1], 1);
    // int t3 = readData(0x90, &calib[2],1);
    // int t4 = readData(0x91, &calib[3], 1);
    // int t5 = readData(0x92, &calib[4],1);
    // int t6 = readData(0x93, &calib[5], 1);
    // int t7 = readData(0x94, &calib[6], 1);
    // int t8 = readData(0x95, &calib[7], 1);
    // int t9 = readData(0x96, &calib[8], 1);
    // int t10 = readData(0x97, &calib[9], 1);
    // int t11 = readData(0x98, &calib[10],1);
    // int t12 = readData(0x99, &calib[11], 1);
    // int t13 = readData(0x9A, &calib[12], 1);
    // int t14 = readData(0x9B, &calib[13], 1);
    // int t15 = readData(0x9C, &calib[14], 1);
    // int t16 = readData(0x9D, &calib[15], 1);
    // int t17 = readData(0x9E, &calib[16], 1);
    // int t18 = readData(0x9F, &calib[17], 1);

    // int err = t1 + t2 + t3 + t4 + t5 + t6 + t7 + t8 + t9 + t10 +
    //         t11 + t12 + t13 + t14 + t15 + t16 + t17 + t18;

    //Store Calibration data
    c.dig_P1 = calib[0] | calib[1] << 8;
    c.dig_P2 = calib[2] | calib[3] << 8;
    c.dig_P3 = calib[4] | calib[5] << 8;
    c.dig_P4 = calib[6] | calib[7] << 8;
    c.dig_P5 = calib[8] | calib[9] << 8;
    c.dig_P6 = calib[10] | calib[11] << 8;
    c.dig_P7 = calib[12] | calib[13] << 8;
    c.dig_P8 = calib[14] | calib[15] << 8;
    c.dig_P9 = calib[16] | calib[17] << 8;

    return 0;

}

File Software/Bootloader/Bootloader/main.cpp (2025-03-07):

#include "mbed.h"
#include "EUSBSerial.h"
#include "FlashIAPBlockDevice.h"
#include <cstdint>
#include <cstdio>
#include <cstring>

#define DEBUG(...) {if (pc != nullptr) {pc->printf(__VA_ARGS__);}}

EUSBSerial* pc = nullptr;


// =============== THREADS ===============
    volatile bool led_running = true;
    void led_indicator() {
        PwmOut led(PB_9);

        bool dir = true;
        float val = 0.5;

        while (led_running) {
            led.write(val);
            if (dir) {
                val += 0.05;
                if (val >= 1.0)
                    dir = false;
            }
            else {
                val -= 0.05;
                if (val <= 0.2)
                    dir = true;
            }

            ThisThread::sleep_for(10ms);
        }

        led.write(0);
    }


    void _setup_watchdog() {
        Watchdog &watchdog = Watchdog::get_instance();
        watchdog.start(30000);
        watchdog.kick();
    }


    void _kick_watchdog() {
        Watchdog &watchdog = Watchdog::get_instance();
        
        if (!watchdog.is_running()){
            watchdog.start(30000);
        }


        while (true) {
            watchdog.kick();
            ThisThread::sleep_for(25s);
        }
    }
// =======================================


bool serial_boot();

int main() {
    // TODO read S1 / S2 first as this will be the flash entry point for radio and MCP
    int boot_status = 0;

    pc = new EUSBSerial(0x3232, 0x0000);

    ThisThread::sleep_for(500ms);
    pc->printf("ID\n");
    ThisThread::sleep_for(500ms);
            
    char buf[6];
    pc->readline(buf, 6);

    if (buf[0] == 'B' &&
        buf[1] == 'O' &&
        buf[2] == 'O' &&
        buf[3] == 'T')
    {
        boot_status = 1;
    }


    Thread t;
    Thread t2;
    if (boot_status != 0) {
        t.start(led_indicator);
        t2.start(_kick_watchdog);
    }

    switch (boot_status) {
        case 1:
            serial_boot();
            break;
        default:
            break;
    }

    if (boot_status != 0) {
        led_running = false;
        t.join();
    }

    if (pc != nullptr)
        delete pc;

    _setup_watchdog();
    mbed_start_application(POST_APPLICATION_ADDR);
}

size_t _serial_get_program_size() {
    pc->printf("SIZE\n");
    ThisThread::sleep_for(10ms);
    char buf[25] = {0};
    pc->readline(buf, 25);

    size_t program_size = 0;
    for (int i = 0; i<25; i++) {
        if (buf[i] < '0' || buf[i] > '9')
            break;
        program_size *= 10;
        program_size += buf[i] - '0';
    }

    return program_size;
}

bool _get_bytes(char* buf, size_t len) {
    pc->printf("DATA\n");
    for (int i = 0; i<len; i++) {
        bool res = pc->get_c(buf+i);
        if (!res)
            return false;
    }
    return true;
}


bool serial_boot() {    
    pc->printf("log: 0x%X | 0x%X\n", POST_APPLICATION_ADDR, POST_APPLICATION_SIZE);
    FlashIAPBlockDevice bd(POST_APPLICATION_ADDR, POST_APPLICATION_SIZE);
    bd.init();


    size_t program_size = _serial_get_program_size();

    pc->printf("log: 0x%X\n", program_size);

    if (program_size > POST_APPLICATION_SIZE) {
        pc->printf("log: ERROR | Application larger than ROM\n");
        return false;
    }

    uint32_t addr = 0;
    char buf[256] = {0};

    while (addr < program_size) {
        if (addr % bd.get_erase_size() == 0) {
            pc->printf("log: erasing block\n");
            bd.erase(addr, bd.get_erase_size());
        }

        memset(buf, 0, 256);

        size_t to_read = (program_size - addr < 256) ? program_size - addr : 256;
        //pc->printf("log:expecting %d bytes\n", to_read);
        if (!_get_bytes(buf, to_read)) {
            DigitalOut errorled(PB_10);
            errorled.write(1);
            pc->printf("log:failed to read ... continuing\n");
            ThisThread::sleep_for(100ms);
            continue;
        }
        //pc->printf("log:got all bytes ... writing\n");

        for (int i = 0; i<to_read; i++) {
            bd.program(&buf[i], addr, 1);
            addr += 1;
        }

        //pc->printf("log:wrote to address 0x%X\n", addr);

        //ThisThread::sleep_for(20ms);
        //pc->printf("log: wrote %d bytes\n", to_read);
    }

    bd.deinit();

    pc->printf("DONE\n");
    return true;
}

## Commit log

2024-08-08 initial commit
    Added folders for hardware and software and copied over RCS board (sarprcs repo).
    [32_768_crystal.STEP, BMP280.step, BNO055.step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]
2024-08-14 removed RCS-specific components
    removed solenoid connectors, SPI connectors, LTC, and extra IMU
    [RCS_Hardware.kicad_pcb, RCS_Hardware.kicad_sch]
2024-08-18 Added GPS and Altimeter to schematic
    still need to add wires
    [RCS_Hardware.kicad_sch]
2024-08-18 changed filenames to ARES_FC (Flight Computer)
    [ARES_FC.kicad_pcb, ARES_FC.kicad_sch]
2024-08-20 started filling out GPS schematic
    [ARES_FC.kicad_sch]
2024-08-21 finished GPS schematic
    [ARES_FC.kicad_sch]
2024-08-27 finished schematic for MBP280, GPS and UARTs
    [ARES_FC.kicad_sch]
2024-08-27 Fixed "RCS Board Problems"
    in RCS Board Problems Discord Thread.
    [ARES_FC.kicad_sch]
2024-09-04 created kicad project for motor control board
    [motor_control_design.kicad_pcb, motor_control_design.kicad_sch]
2024-09-06 Seperated lines that were previously merged All UART devices were on the same bus and have since been moved to GPS_UART and RADIO_UART Motor UART has been replaced with I2C NRST lines have been seper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
    [main.cpp]
2024-09-06 Converted BMP280 to I2C was wrongly setup as SPI
2024-09-06 forgot to save everything before last commit
    [ARES_FC.kicad_sch]
2024-09-06 added edges and screw hole layout for 60mm board
    [ARES_FC.kicad_pcb]
2024-09-11 Routing 75% complete
    added all footprints and connected most components
    [ARES_FC.kicad_pcb, ARES_FC.kicad_sch, CD-PA1616D.step]
2024-09-12 Fixed PCB Edge
    [ARES_FC.kicad_pcb]
2024-09-12 routing 99% done
    double check external antenna connector. S1 & S2 unused for ribbons. DRC not completed.
    [ARES_FC.kicad_pcb, ARES_FC.kicad_sch]
2024-09-12 DRC fixes
    [ARES_FC.kicad_pcb]
2024-09-12 Antenna and Model Changes Added Fencing Vias to Ext. GPS Antenna Added 3D Models for Ribbon Connectors and GPS
    [ARES_FC.kicad_pcb, ARES_FC.kicad_sch, AdafruitGPSv2.step]
2024-09-15 Motor Control Base Setup Copied Base STM32 schema from Flight Computer Project Copied and Modified Edge Cuts from Flight Computer Added LM2576 Schematic
    [motor_control_design.kicad_pcb, motor_control_design.kicad_sch]
2024-09-15 Added Vbat Sensing schema to motor board
    [motor_control_design.kicad_sch]
2024-09-15 fixed ribbon connectors and S1 & S2
    [ARES_FC.kicad_pcb, ARES_FC.kicad_sch]
2024-09-16 tiny routing change for aesthetic purposes
    [ARES_FC.kicad_pcb]
2024-09-16 Added both H-Bridge schemas (pending testing)
    [motor_control_design.kicad_sch]
2024-09-17 Finished motor controller schematic and routing
    [32_768_crystal.STEP, BMP280.step, BNO055.step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]
2024-09-18 Updated Motor control schema and routing to match new hbridge design
2024-09-18 added motor board renders
2024-09-18 Cleaned up motor board schema
    [motor_control_design.kicad_pcb, motor_control_design.kicad_sch]
2024-09-20 Uploaded CAD for all 3 boards
2024-09-20 Motor Board: Added LCSC Part Numbers Fixed missing ground on diode
    [motor_control_design.kicad_pcb, motor_control_design.kicad_sch]
2024-09-29 added most part numbers
    [ARES_FC.kicad_sch, FC_JLCPCB_BOM.xls]
2024-09-30 Motor Board: Optimized LM2576 circuit - bigger capacitor - better inductor Added assembly files (outdated)
    [IND_MWSA1206S_SNL.step, bom.csv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]
2024-10-01 added U.FL part number
    [ARES_FC.kicad_pcb]
2024-10-01 added tentative external i2c connectors
    [ARES_FC.kicad_pcb, ARES_FC.kicad_sch, BM04B-SRSS-TB_LF__SN_.step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]
2024-10-02 fixed motor conn. i2c and external i2c conn.s, changed PNs, added models
    new PN for Y2, added 3D models for BMP, Antenna, and ext. i2c connectors.
    [ARES_FC.kicad_pcb, ARES_FC.kicad_sch, BM04B-SRSS-TB-LF--SN---3DModel-STEP-56544.STEP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]
2024-10-11 added BOMs
    [ARES_FC-B_Cu.gbr, ARES_FC-B_Mask.gbr, ARES_FC-B_Paste.gbr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]
2024-11-07 Added Via Stiching and ViPs to Motor Board
    [motor_control_design.kicad_pcb, motor_control_design.kicad_sch]
2024-11-07 Added Fencing Vias and ViPs to FC
    [ARES_FC.kicad_pcb]
2024-11-07 Removed front copper traced under GPS Increased GPS feed line width to be 50ohm Curved GPS feed line to reduce emmisions
    [ARES_FC.kicad_pcb]
2024-11-08 Updated CAD and added Renders
2024-11-11 aesthetic edits (silkscreen, etc.)
    [ARES_FC.kicad_pcb, ARES_FC.kicad_sch]
2024-11-11 connected GPS_NRST to STM32
    [ARES_FC.kicad_pcb, ARES_FC.kicad_sch]
2024-11-11 some LCSC Part (BOM) changes; more needed.
    [ARES_FC-B_Cu.gbr, ARES_FC-B_Mask.gbr, ARES_FC-B_Paste.gbr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]
2024-11-12 changed C4 to 0603; removed vias on pads; added stitching vias
    [ARES_FC.kicad_pcb]
2024-11-13 fixed JLC part numbers and ran DRC
    [ARES_FC-B_Cu.gbr, ARES_FC-B_Mask.gbr, ARES_FC-B_Paste.gbr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]
2024-11-13 some DRC warnings fixed
    [ARES_FC.kicad_pcb]
2024-11-13 Added more stitching vias to cutoff segments of ground plane Shrunk ViPs from 0.6/0.3 to 0.4/0.2
    [ARES_FC.kicad_pcb]
2024-11-13 hid silkscreen component labels
    [ARES_FC-B_Cu.gbr, ARES_FC-B_Mask.gbr, ARES_FC-B_Paste.gbr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]
2024-11-14 initialize data analysis folder
    [ARES_FC.csv, ARES_FC_BOM.csv, AdafruitGPSv2.step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]
2024-11-21 added missing 3.3V bridge connection to GPS PS pin
    [ARES_FC.kicad_pcb, ARES_FC.kicad_sch]
2024-11-29 added gsim testing folder and did some sim stuff
    [ARES_FC_BOM.csv]
2024-11-29 plot input break and output ang. velocity
2024-12-07 initialize FC and MCPS software folder
    [app_hook.xml, mbed_os-usb_test_device1.cfg, mbed_os-usb_test_device2.cfg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]
2024-12-13 lowkey forgor ... I think assembly files for motor board
    [cpl.csv, motor_control_design-B_Cu.gbr, motor_control_design-B_Mask.gbr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]
2024-12-14 MCP_Testing codebase initial commit target configuration base led and motor1 simple control code
2025-01-11 PullTab PCB schematic, layout, gerbers, and prints
    [pulltab-B_Cu.gbr, pulltab-B_Mask.gbr, pulltab-B_Silkscreen.gbr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]
2025-01-18 fixed pulltab mosfet pin orientation added cad
    [pulltab.kicad_pcb, pulltab.kicad_sch, pulltab.step]
2025-01-18 blackpill setup
    [FC_Testing_map.csv]
2025-01-21 setup blackpill target again
    [FC_Testing_map.csv, app_hook.xml, mbed_os-usb_test_device1.cfg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]
2025-01-28 Corrected TF and closed simulink ctrl loop
    added zero to TF and started tuning PID in system_tf.slx
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2025-02-08 Implemented starting point for GPS Driver Fixed missing file issues in blackpill build target Added EUSBSerial class for better USBSerial support Updated main.cpp with working examples
    [main.cpp]
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2025-02-26 can print message to port, debugging update() function
2025-03-06 motor control PID
    Created motor controller pid class and created an example in main
2025-03-07 Updated with temperature conversion (error)
    [BMP280.cpp]
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
